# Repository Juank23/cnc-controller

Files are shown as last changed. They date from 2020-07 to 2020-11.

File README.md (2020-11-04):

Контроллер ЧПУ
==============

GRBL контроллер на плате ESP32. Применяется для фрезерного станока, 3D-роутера, 3D-принтера, лазерного резака, винилового резака, плазменного резака с ЧПУ. Почитать подробнее можно на [тут](https://github.com/bdring/Grbl_ESP32_MPCNC_Controller).

Я использую для небольшого ЧПУ станка для хоббийных дел **T8 DIY CNC Engraver**.

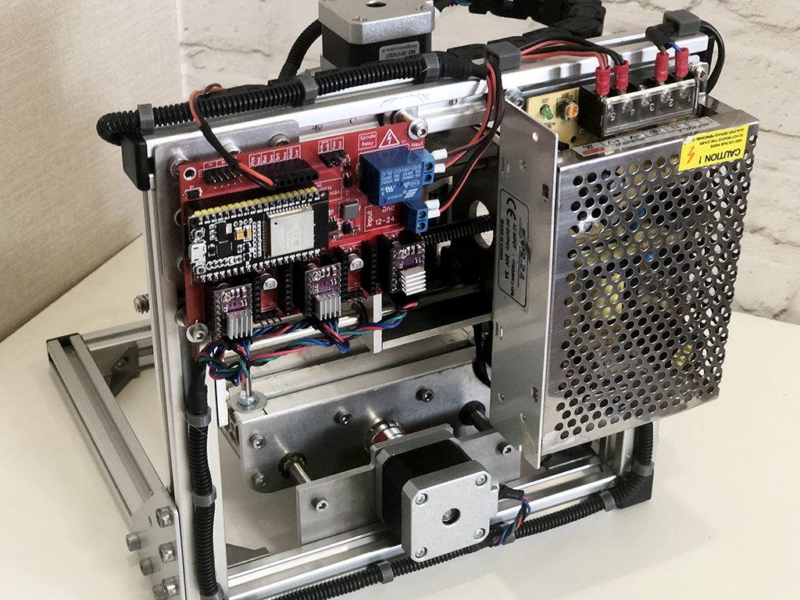
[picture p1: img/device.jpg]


## Плата

| Верх | Низ
|---|---
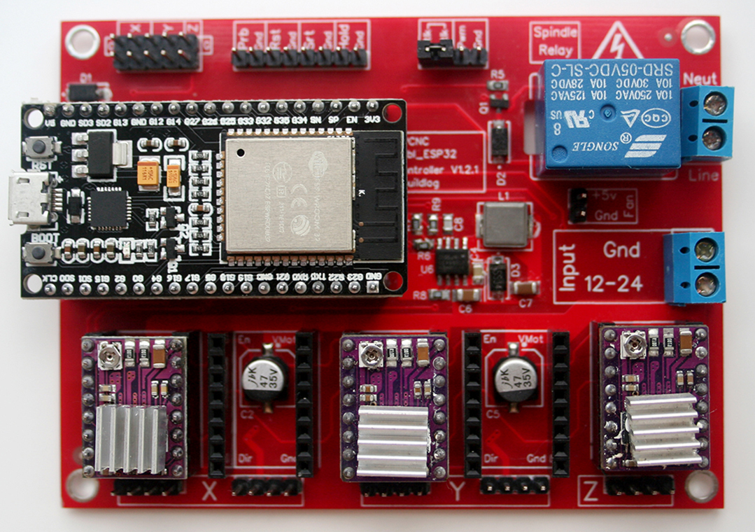
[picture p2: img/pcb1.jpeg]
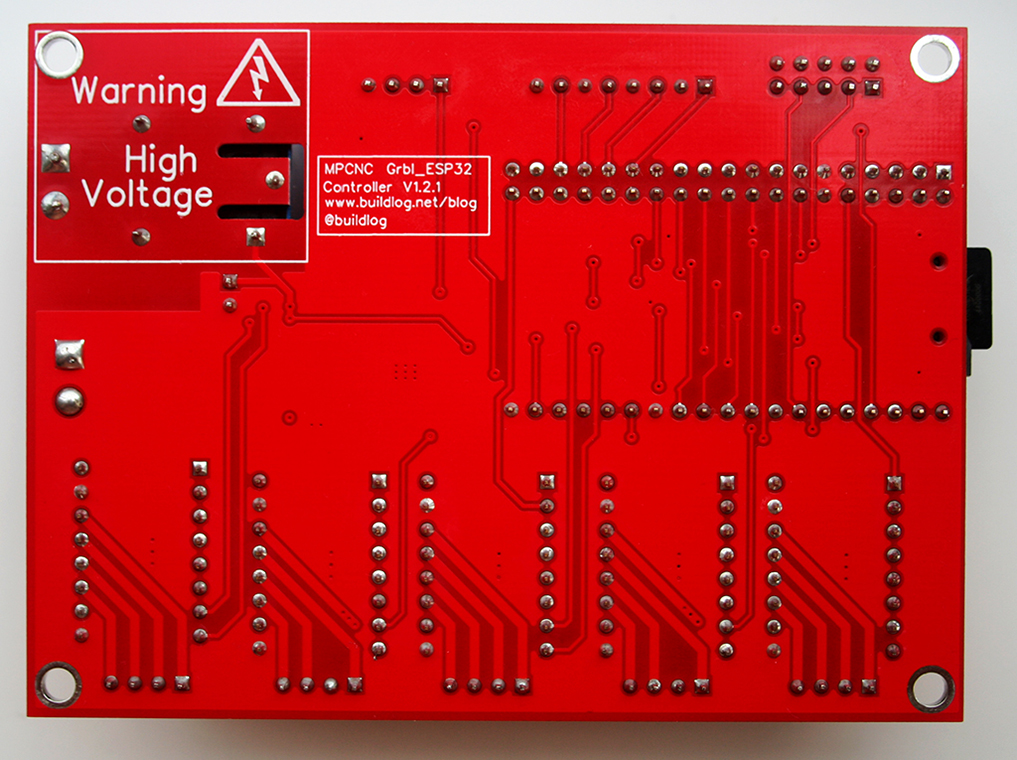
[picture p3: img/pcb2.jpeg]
|  | 

## BOM:

|Name|Desc|Value
|---|---|---
|C1, C2, C3, C5, C9|Capacitor, Electrolytic|47u 35V
|C4|Capacitor Ceramic|100nF 50V
|C6|Capacitor Ceramic|10uF
|C7|Capacitor Ceramic|22uF 6.3V
|C8|Capacitor Ceramic|150pF 50v 0805
|D1, D2, D3|Diode Schottkey|3A
|J1|Connector Header|Male 1x8 0.1
|J2, J4, J6, J7, J9, J11|Connector Header|Male 1x4 0.1
|J3|Connector Header|Male 2x5 0.1
|J8|Connector Header|Male 1x2 0.1
|J10|Socket Micro SD|TF-01A
|K1|Relay|5V
|L1|Inductor|4.7uH 5.5A
|Q1|Transistor|NPN 0.5A
|R1, R2, R3, R4, R10|Resistor|10k
|R5|Resistor|1K
|R6|Resistor|210k
|R7|Resistor|40.2k
|R8, R9|Resistor|100k
|TB1, TB2|Terminal Block|1x2 5mm Blue
|U1, J5|Connector Header|ESP-32 Female 1x19 0.1
|U2, U3, U4, U5, U7|Connector Header|Female 1x8 0.1
|U6|DC-DC Power Supply Controller|MP1584EN
|U8|Voltage level Shifter|TXS0101DBVR

## Прошивка в Arduino IDE

- При первой заливке скетча Grbl_Esp32 в ESP32 убедитесь, что он не вставлен в плату контроллера!
- JSON файл (Пакет **esp32**): ```https://raw.githubusercontent.com/espressif/arduino-esp32/gh-pages/package_esp32_index.json```
- Выбираем плату **ESP32 Dev Module** и схему **Minimal SPIFFS (1.9MB APP с OTA / 190KB SPIFFS)** в меню "Инструменты":

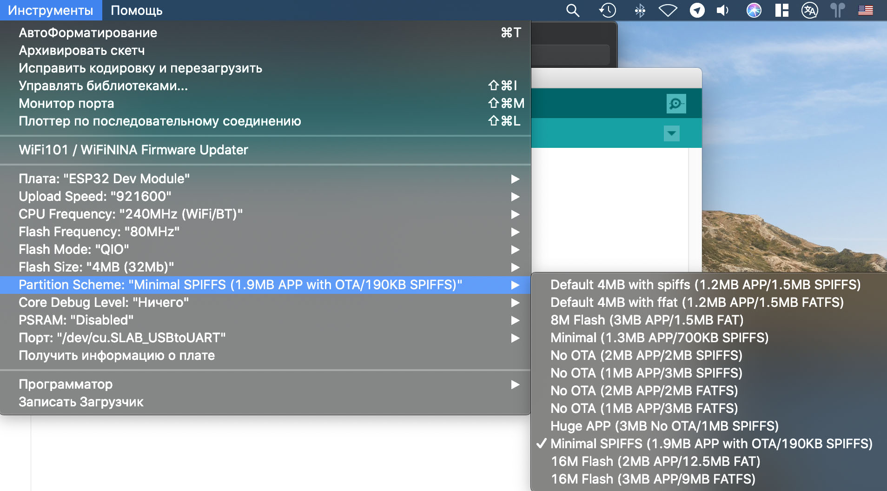
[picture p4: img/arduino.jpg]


- Компилируем **Grbl\_Esp32/Grbl\_Esp32.ino**
- Загружаем. При появлении ```Connecting........``` нужно удерживать кнопку "BOOT" на плате ESP32. При нормальной загрузке должно быть: ```Leaving... Hard resetting via RTS pin...```
- Проверяем настройки в "Мониторе порта". Нажимаем RESET на плате и видим:

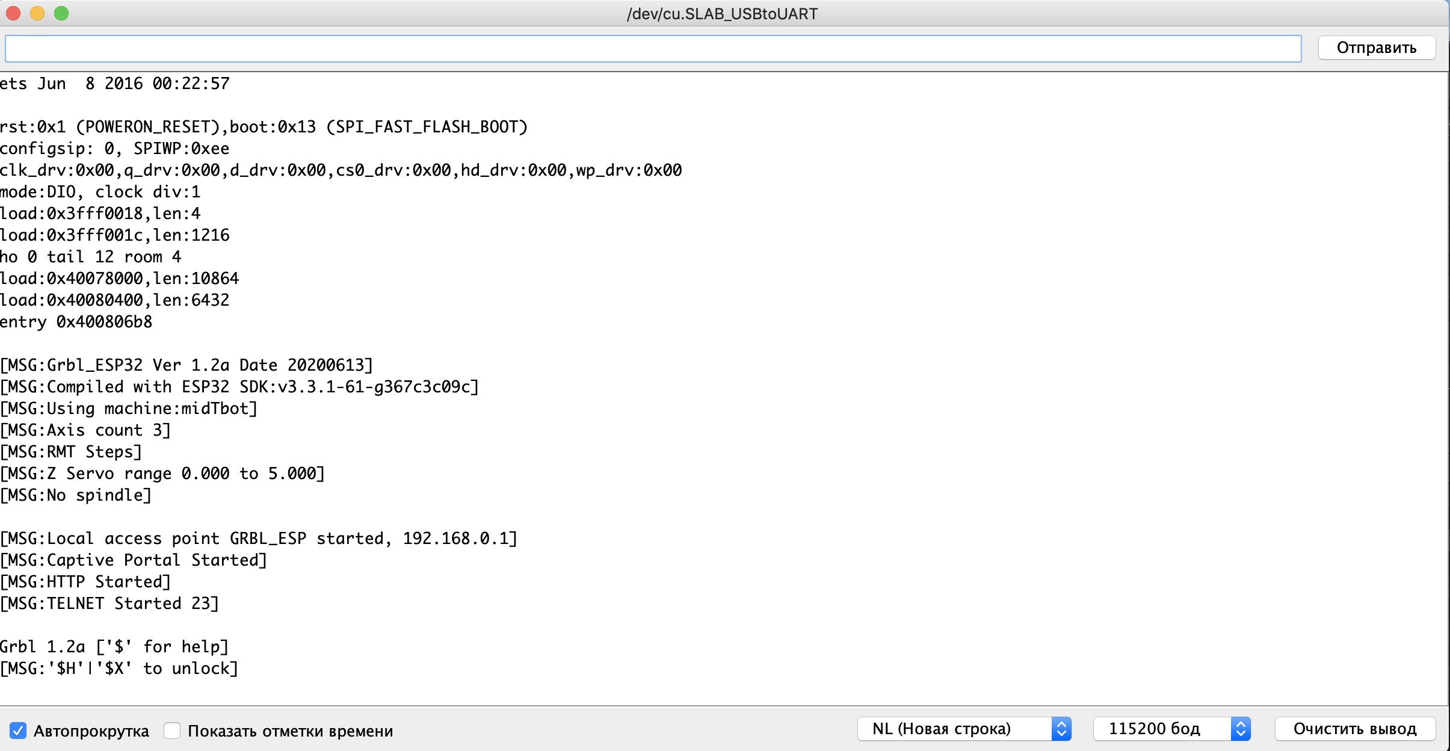
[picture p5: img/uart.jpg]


## Настройка моторов

- Если моторы имеют неверное вращение, то разворачиваем разъем на 180 градусов
- Сбрасываем по умолчанию ```$rst = $```
- Проверка на парковку: ```$H```
- Установка тока двигателя для мотора **NEMA 17** (1,5A): 

A4988:

```
Vref = Current Limit * 8 * 0,100(RS) = 1,5 / 1,25 = 1,2V
```

DRV8825 (на 70%):

```
Vref = Imax / 2 = 0,7 * 1,5 / 2 = 0,5V
```

## WebUI (Wi-Fi)

При первом включении будет создана точка доступа Wi-Fi со следующими настройками:

- SSID: ```GRBL_ESP```
- Пароль: ```12345678```
- IP-адрес : ```192.168.0.1```

Нужно подключится и загрузить файл данных ```Grbl_Esp32/data/index.html.gz```, содержащий веб-интерфейс.

Если скомпилировали прошивку с помощью ```ENABLE_AUTHENTIFICATION``` в ```config.h```, WebUI будет иметь двух пользователей с именами "admin" и "user". Если входим как "admin/admin", то  можем изменить любой параметр. Если вы вошли как "user/user", можем взаимодействовать только с Grbl. (Имена пользователей и пароли можно настроить перед компиляцией, отредактировав config.h).

Далее в **WebUI** нужно настроить как Wi-Fi клиент, а не точка доступа.

## Bluetooth

Как настроить написано тут: https://github.com/bdring/Grbl_Esp32/wiki/Using-Bluetooth

## Создание G-Code

Есть очень много программ для создания G-Code. Пользуйтесь к которой привыкли.

Далее закадываем файл на карту памяти и в **WebUI** выбераем его.

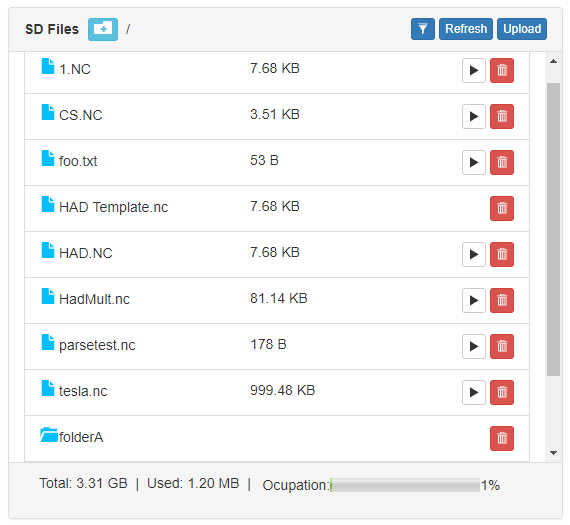
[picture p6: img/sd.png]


## Охлаждение

Если плата или драйвера шаговых двигателей греются, то можно распечатать держатель вентилятора охлаждения на 5в.

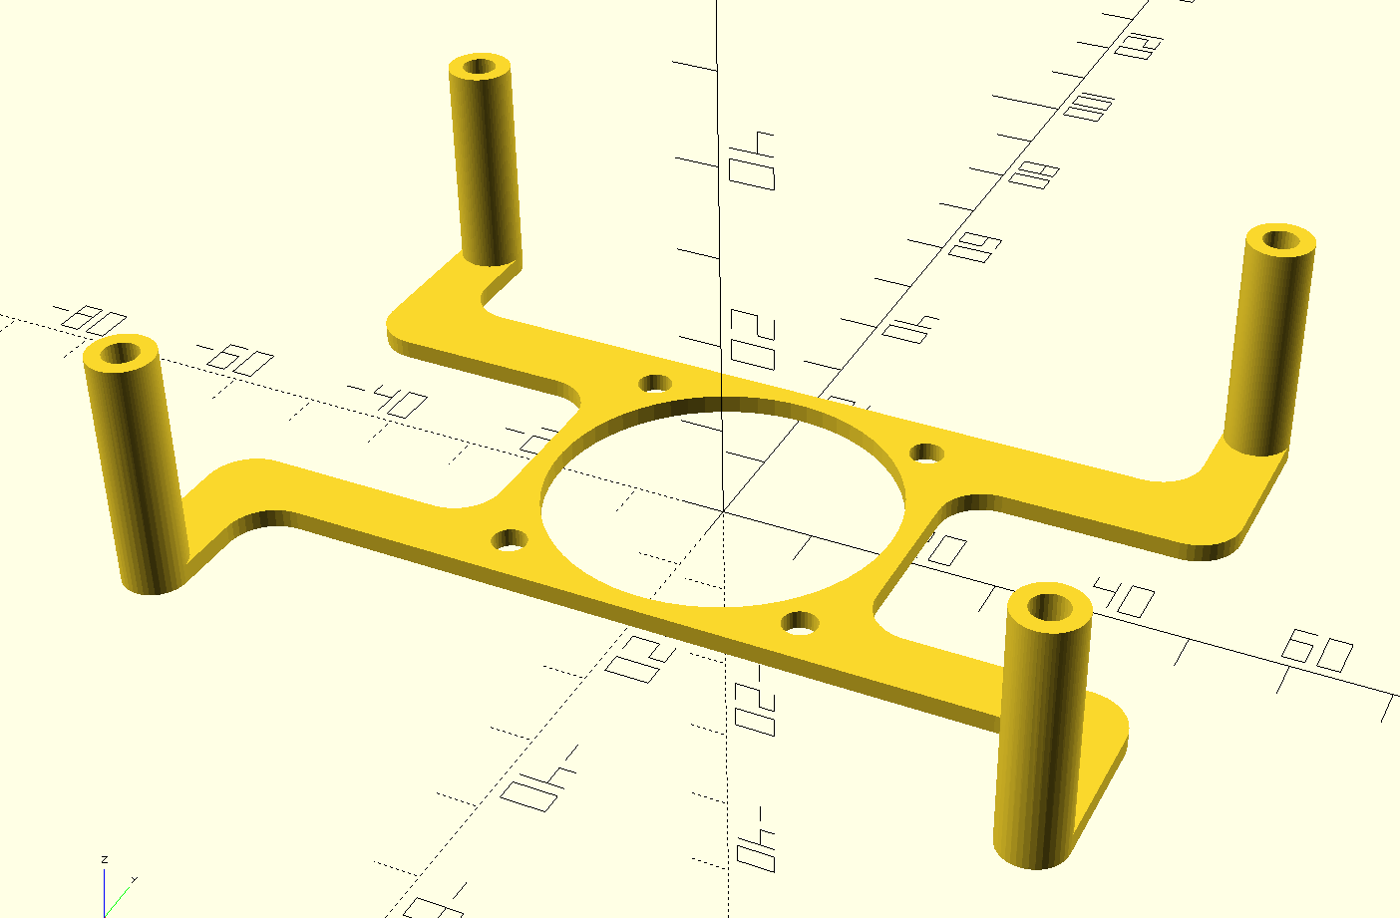
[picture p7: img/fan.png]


## Контакты

GitHub автора: [https://github.com/bdring/Grbl_ESP32_MPCNC_Controller](https://github.com/bdring/Grbl_ESP32_MPCNC_Controller)

Grbl Esp32: [https://github.com/bdring/Grbl_Esp32](https://github.com/bdring/Grbl_Esp32)

Связаться со мной: info@dementiev.net

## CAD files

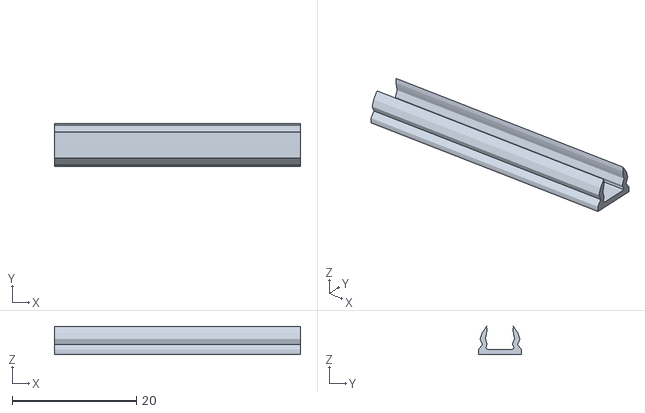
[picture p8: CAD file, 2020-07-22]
3d print/cover.stl
39.6 x 6.97 x 4.51

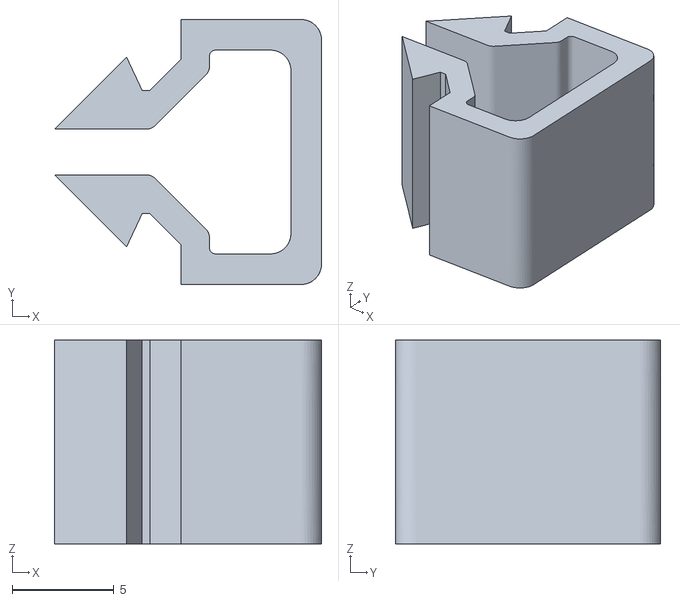
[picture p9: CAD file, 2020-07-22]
3d print/сlip_1.stl
13.1 x 13.0 x 10.0

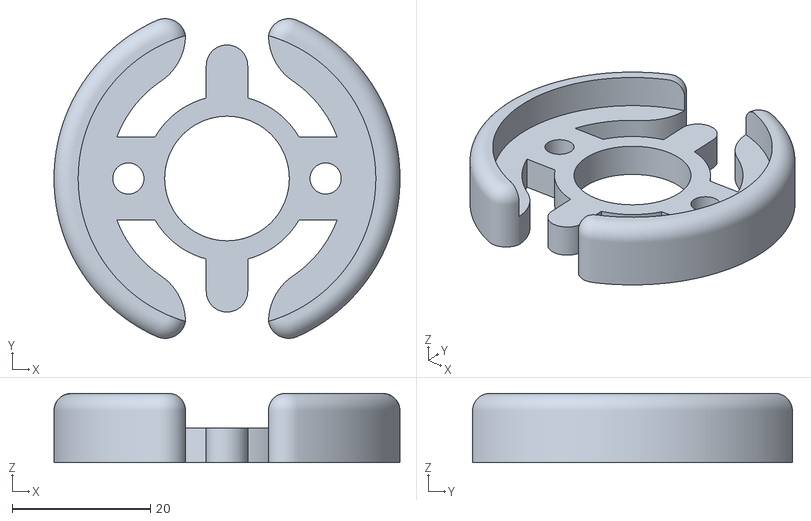
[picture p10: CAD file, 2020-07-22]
3d print/spindle_motor_fan.stl
50.0 x 46.2 x 10.0

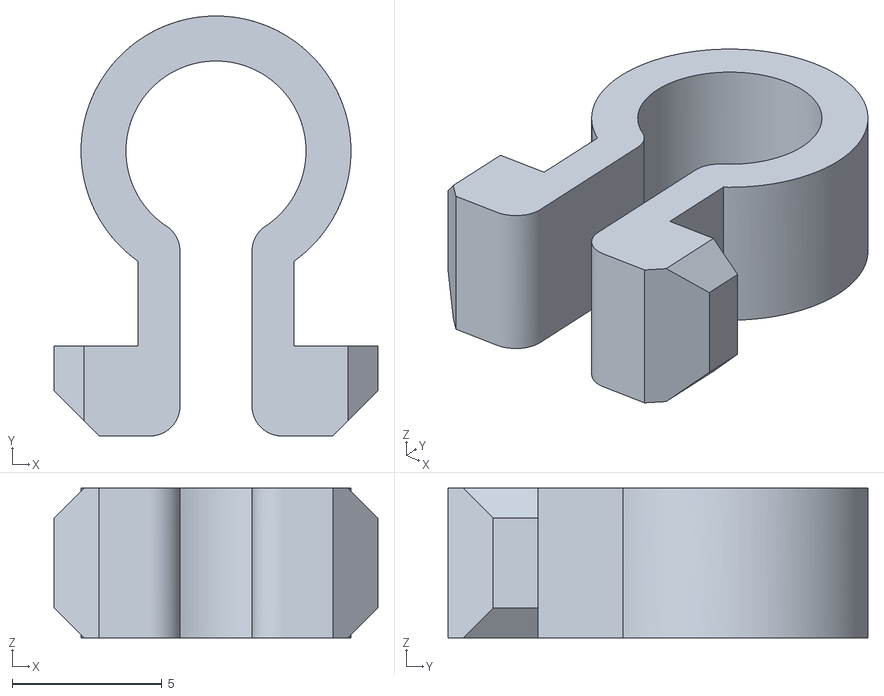
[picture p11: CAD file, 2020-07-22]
3d print/сlip_2.stl
10.8 x 14.0 x 5.00

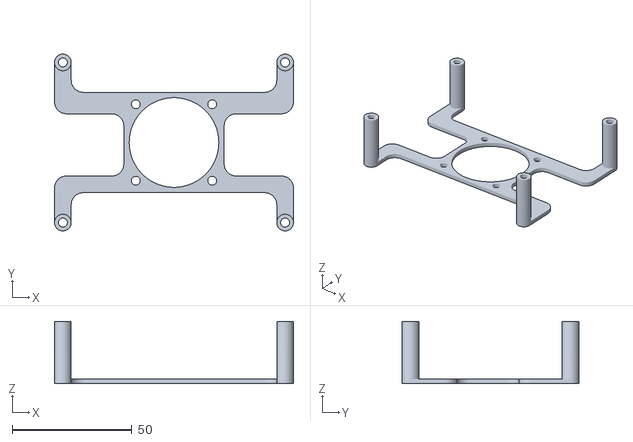
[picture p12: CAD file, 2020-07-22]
3d print/fan_mount.stl
100.0 x 74.0 x 26.0

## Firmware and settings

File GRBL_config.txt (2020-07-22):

$0=3
$1=255
$2=0
$3=0
$4=0
$5=1
$6=0
$10=1
$11=0.010
$12=0.002
$13=0
$20=0
$21=0
$22=1
$23=3
$24=100.000
$25=200.000
$26=250
$27=2.000
$30=1.000
$31=0.000
$32=0
$100=1600.000
$101=1600.000
$102=1600.000
$110=500.000
$111=500.000
$112=500.000
$120=10.000
$121=10.000
$122=10.000
$130=130.000
$131=110.000
$132=45.000

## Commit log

2020-07-22 Первое размещение
    [GRBL_config.txt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]
2020-11-04 Поменял описание
